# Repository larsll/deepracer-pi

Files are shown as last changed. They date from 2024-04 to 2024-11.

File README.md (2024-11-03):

The effort has moved to [DeepRacer Custom](https://github.com/aws-deepracer-community/deepracer-custom)!

# DeepRacer for Raspberry Pi 4

This repository provides a port of the DeepRacer software stack to the Raspberry Pi 4. It runs
on Ubuntu 22.04 with ROS2 Humble, but with most of original code. To make the image smaller the server image is recommended.

## Features

Main features of the port:

- Previously trained models will work
- Uses Tensorflow Lite or OpenVINO for inference. Supports the Intel Neural Compute Stick 2 (NCS2/MYRIAD)
- Can integrate with DREM
- Single power source¹ - reduces weight and lowers center of gravity
- Over-the-Air Software Updates

## Parts

The following parts are needed:

- Raspberry 4 or compatible board, recommended 4GB or 8GB RAM, but even 1GB will work as memory consumption is about 700MB.
- Optional: [Intel Neural Compute Stick (NCS) 2](https://www.intel.com/content/www/us/en/developer/articles/tool/neural-compute-stick.html)
- [Waveshare Servo Driver Hat](https://www.waveshare.com/product/raspberry-pi/hats/motors-relays/servo-driver-hat.htm) or compatible PCA9865 servo boards.
- USB camera with ~60 deg FOV, e.g. original DeepRacer camera or a Raspberry Pi camera.
- 4 RGB light diodes
- Misc cables

¹ The Waveshare hat comes with a step-down converter from 7.4V to 5V, and will power the Pi via the GPIO header. Other similar cards will require separate power.

**Optional**

- Fan/heat-sink kit for Raspberry PI 4

## Software Install

Installation of software is reasonably straight forward, as pre-built packages are provided:

- Flash an SD card with Ubuntu 22.04 Server for ARM64 using the Raspberry Pi Imager.
- Boot the SD card, and let it upgrade (this takes some time...)
- Run `git clone https://github.com/larsll/deepracer-pi`
- Run `sudo ./install-prerequisites.sh`
- Reboot
- Run `sudo ./install-deepracer.sh`

Once installed you can start the stack with `sudo /opt/aws/deepracer/start_ros.sh`. To ensure a smooth start a camera needs to be plugged in.
The launch log will now display in the console.

To automatically start at boot do `sudo systemctl enable deepracer-core` and to start the service in the background `sudo systemctl start deepracer-core`.

### Changes

Some changes have been made to the code to enable access to GPIO as sysfs layout is different on the Raspberry Pi than on the custom Intel board.

### Improvements

- Stripped down OS
- Runs the custom deepracer stack also seen in [deepracer-scripts](https://github.com/davidfsmith/deepracer-scripts).

### Details

**PWM Outputs**

| Channel | Purpose | Notes |
| --- | --- | --- |
| 0 | Speed controller | <span style="color:red">Remove red cable for stock DeepRacer ESC</span> |
| 1 | Steering servo | |
| 2 | RGB LED | Tail light - Red |
| 3 | RGB LED | Tail light - Green |
| 4 | RGB LED | Tail light - Blue |
| 5 |
| 6 |
| 7 | RGB LED |
| 8 | RGB LED |
| 9 | RGB LED |
| 10 | RGB LED |
| 11 | RGB LED |
| 12 | RGB LED |
| 13 | RGB LED |
| 14 | RGB LED |
| 15 | RGB LED |

<span style="color:red">**NOTE:** Remove the red cable on the stock DeepRacer from the speed controller into PWM channel 0, otherwise you are putting 6V into the servo hat.</span>

LiPo can power both the board and car, 3 pin (balance lead) gets wired to VIN (black and red cables only) to power the board and RPi. The 2 pin power cable goes to the car as normal.

**GPIO layout:**

- `gpio1` - enables PWM (does not do anything, PWM is always on for the Waveshare board)
- `gpio495`-`gpio504` - maps to PWM7 to PWM15 on the Hat, to control three RGB leds (those originally on the side of the board)

**USB host mode:**
To connect the USB-C port on the Raspberry Pi 4 to a USB on your computer, then you need to perform two changes:
* Add `dtoverlay=dwc2,dr_mode=host` to your `/boot/firmware/config.txt`
* Add `modules-load=dwc2,g_ether` to your `/boot/firmware/cmdline.txt`

With this you will see a new network connect appear in Windows (and Mac?). The Raspberry Pi will have IP 10.0.0.1; you can connect to the console via `https://deepracer.aws`. This will require your computer to be disconnected from all other networks (given a DNS priority issue). SSH directly to the IP will work.

## What does not (yet) work

- Battery gauge is not connected - red warning message persists
- Device Info Node is looking in non-existent places - no real impact

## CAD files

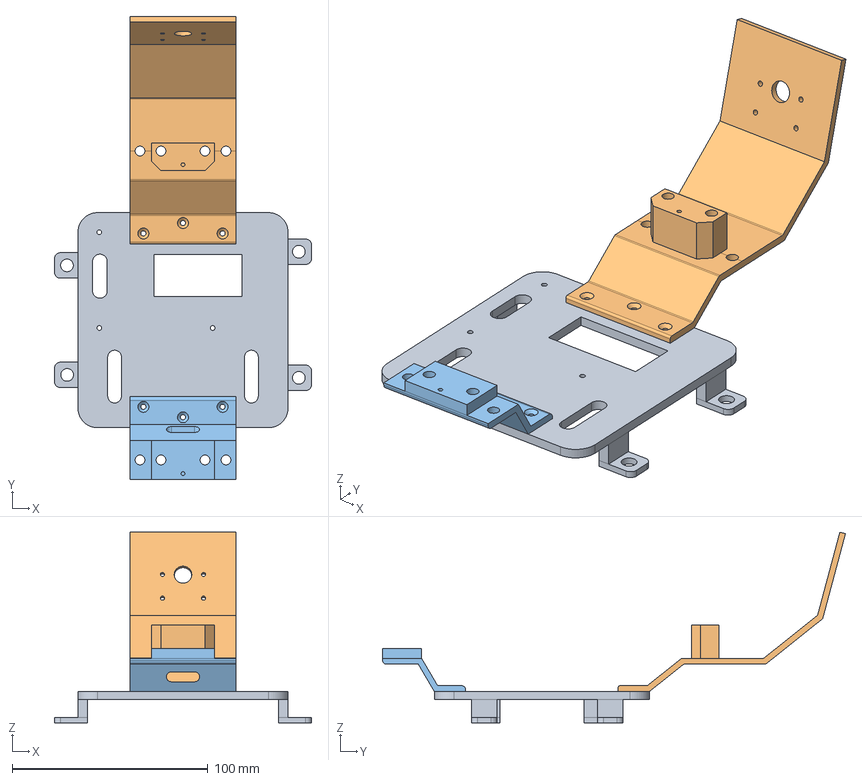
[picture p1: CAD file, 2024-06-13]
drawings/PiMount v1.3.FCStd
131.5 x 236.8 x 97.5 mm
Plate
Front
Back

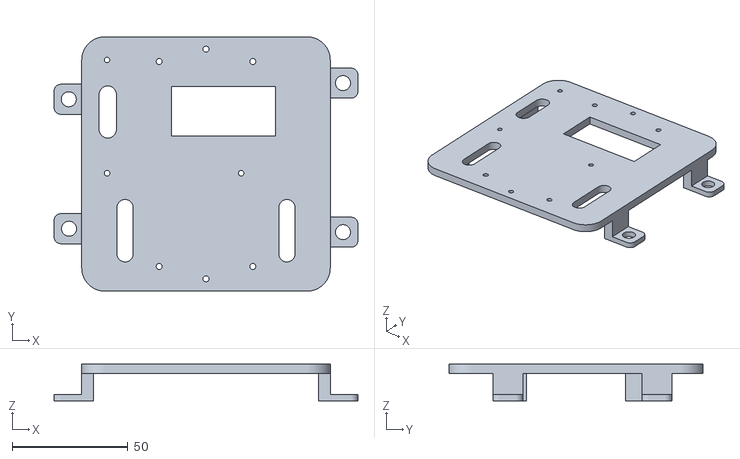
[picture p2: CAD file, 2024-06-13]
drawings/PiMount v1.3-Plate.stl
131.5 x 110.0 x 16.0

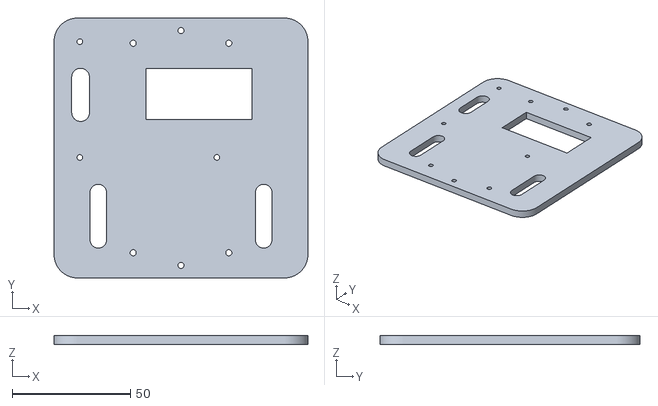
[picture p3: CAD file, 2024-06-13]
drawings/PiMount v1.3-Plate-NoLegs.stl
107.5 x 110.0 x 4.00

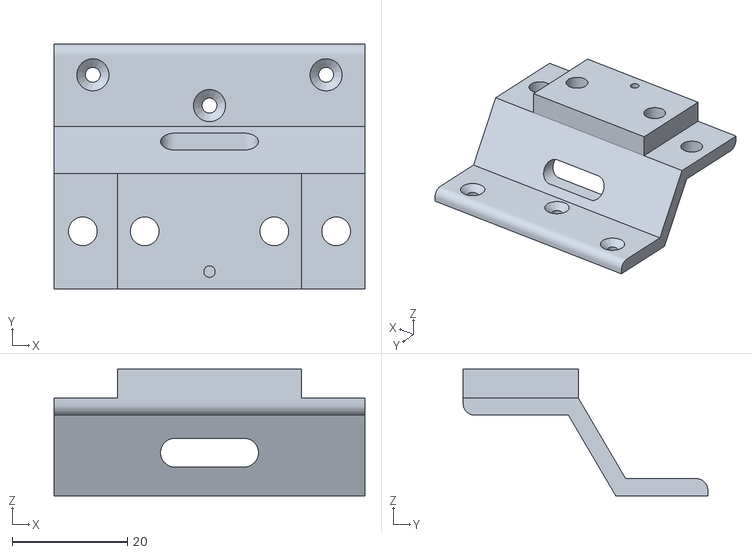
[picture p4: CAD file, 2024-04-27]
drawings/PiMount v1.3-Back.stl
54.0 x 42.5 x 22.0

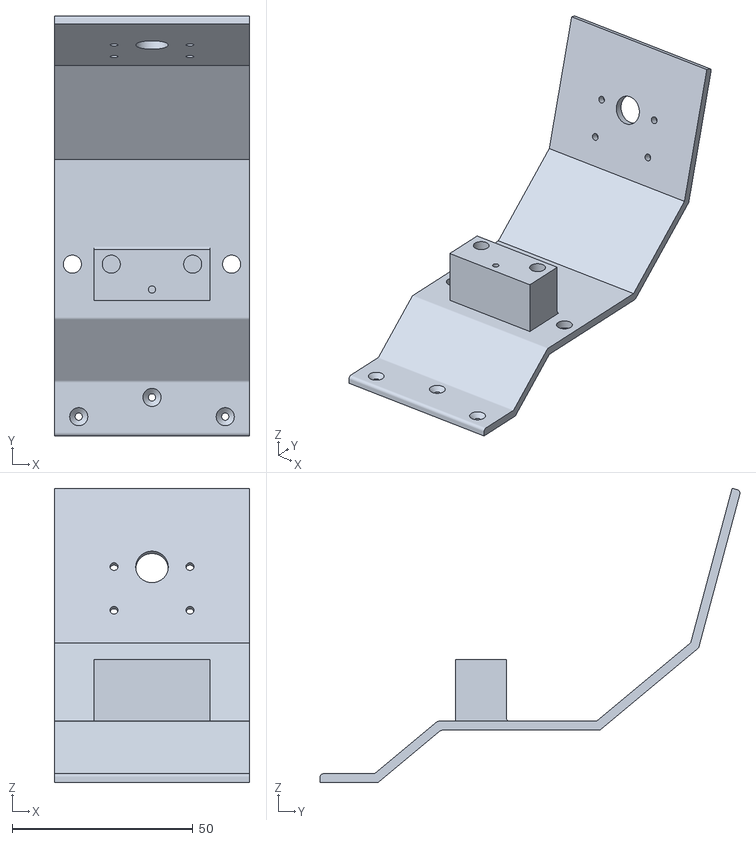
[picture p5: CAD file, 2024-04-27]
drawings/PiMount v1.3-Front.stl
54.0 x 116.1 x 81.4

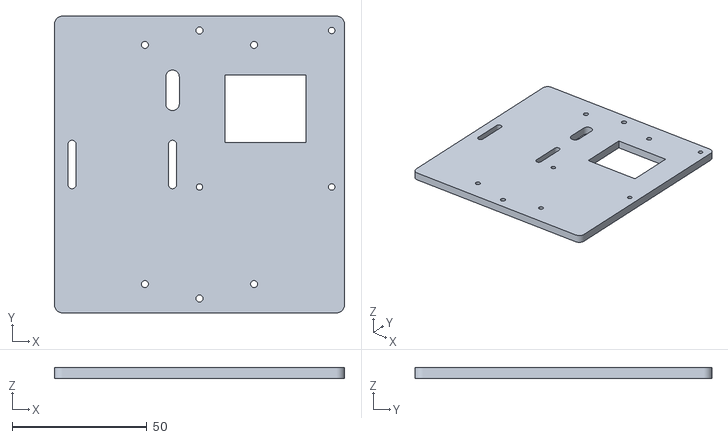
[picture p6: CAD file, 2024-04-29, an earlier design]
drawings/PiMount v1.2-Plate-NoLegs.stl
107.5 x 110.0 x 4.00

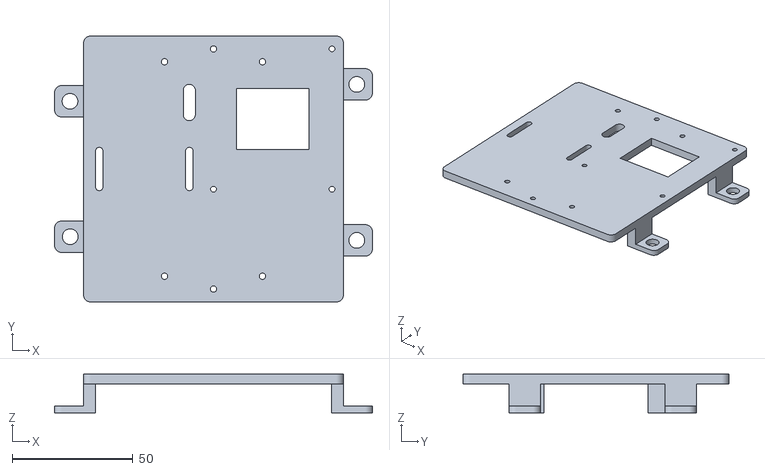
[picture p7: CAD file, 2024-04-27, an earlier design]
drawings/PiMount v1.2-Plate.stl
131.5 x 110.0 x 16.0

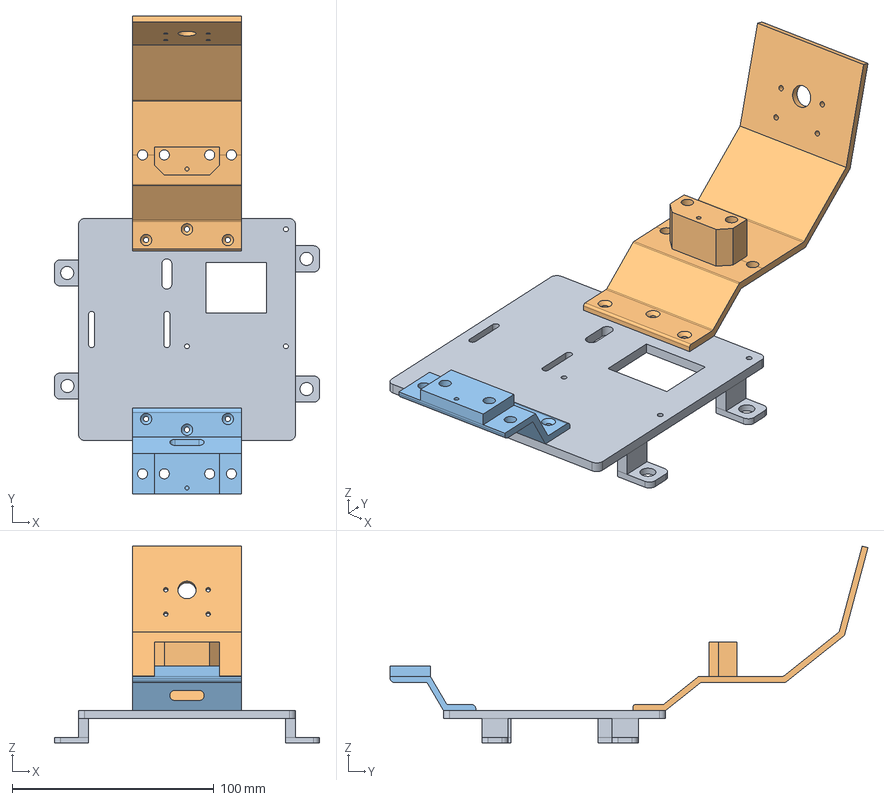
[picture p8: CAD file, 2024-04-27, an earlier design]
drawings/PiMount v1.2.FCStd
131.5 x 236.8 x 97.5 mm
Plate
Front
Back

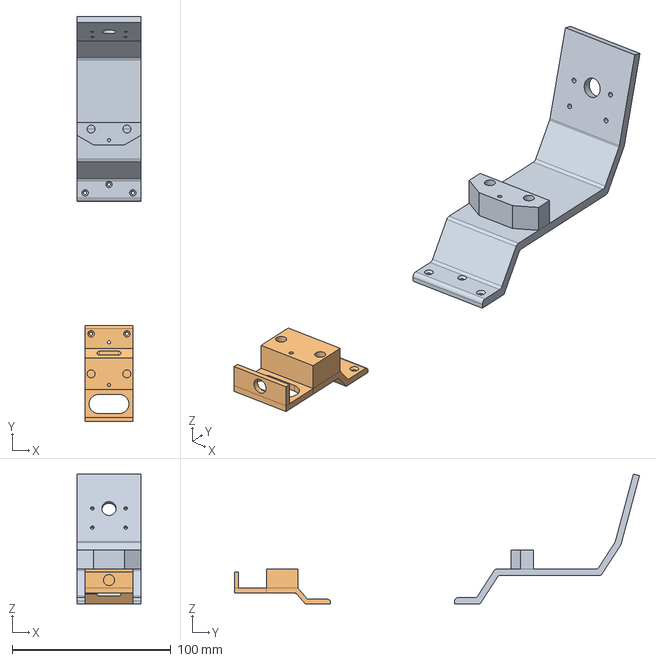
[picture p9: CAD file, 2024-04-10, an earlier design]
drawings/PiMount v1.1.FCStd
40.0 x 254.8 x 81.8 mm
Front
Back

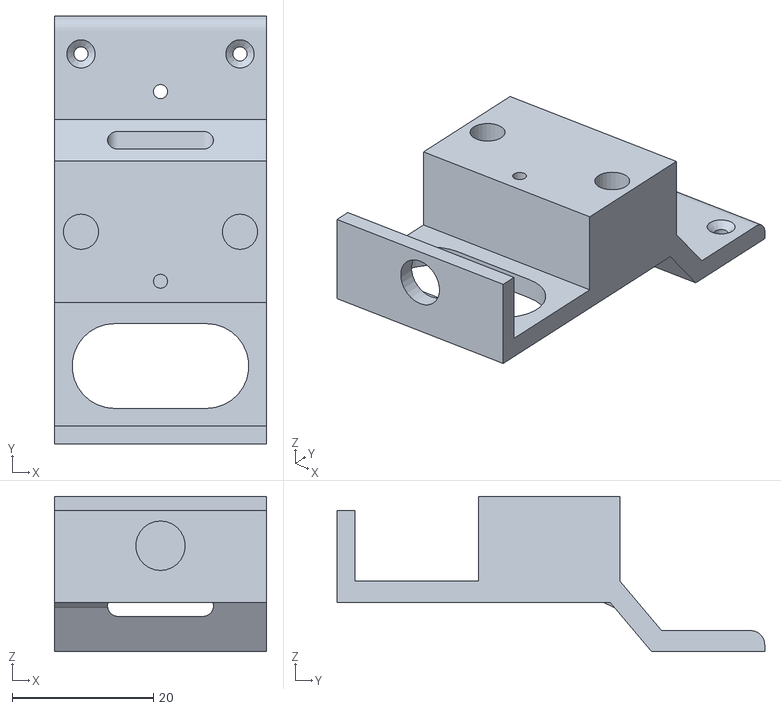
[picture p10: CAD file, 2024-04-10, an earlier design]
drawings/PiMount v1.1-Back.stl
30.0 x 60.5 x 22.0

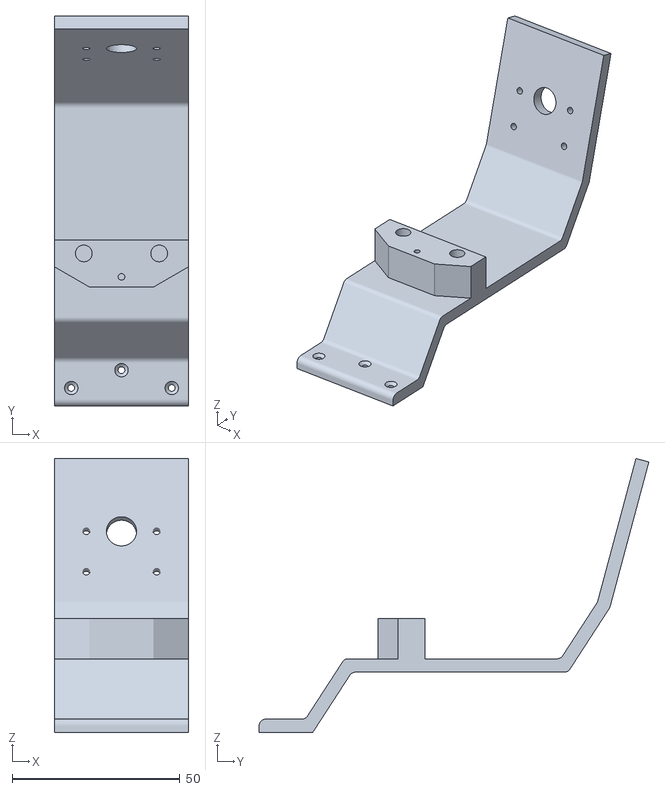
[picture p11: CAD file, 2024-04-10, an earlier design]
drawings/PiMount v1.1-Front.stl
40.0 x 116.3 x 81.8

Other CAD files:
drawings/PiMount v1.1-Plate.stl

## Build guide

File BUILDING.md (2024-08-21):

# Building a Deepracer Pi

* Raspberry Pi 4, recommended 2GB or more of RAM
    * Stand-off set (2.5mm)
* [Waveshare Servo Driver Hat](https://www.waveshare.com/product/raspberry-pi/hats/motors-relays/servo-driver-hat.htm) or compatible PCA9865 servo boards. 
    * Stackable header 40pin (to get higher servo driver hat higher than the fan)
* Raspberry Pi Camera 2
    * Longer cable (20-25cm)
    * Screws M2x15mm + nuts
* Recommended cooling fan: [GeeekPi Raspberry Pi 4 Armor Lite](https://www.amazon.de/gp/product/B091L1XKL6/ref=ppx_yo_dt_b_search_asin_title?ie=UTF8&psc=1)
* RGB Led: 
    * [AZDelivery 5 x KY-016 FZ0455](https://www.amazon.co.uk/AZDelivery-KY-016-3-Colour-Arduino-including/dp/B07V6YSGC9/ref=sr_1_1)
    * 4 female-female jumper cables
    * [Led Holder](https://www.amazon.co.uk/Chanzon-Holder-Headfor-Emitting-Diodes/dp/B083Q9Q1ZR/ref=sr_1_4_sspa)
* Servo extension cable (with red cable cut)
* 3-pin female JST
* 2.5mm plastic screws (preferrably of good quality) to mount back and front; or use M2 screws with nuts

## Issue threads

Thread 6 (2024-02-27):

Abount Hardware,such as camera

Trz-me, 2024-02-27:
Greetings,

Your project has piqued my interest immensely, and I find the prospect of miniaturizing DeepRacer particularly intriguing. Could you please inform me if there are any specific requirements regarding the hardware composition and cable connections for this project?

For instance, is it imperative to use the official DeepLens camera?

The following image depicts a mini DeepRacer model vehicle I previously encountered, which base on  Raspberry Pi.
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

larsll, 2024-02-27:
I have added a Raspberry Pi Camera v2 on mine; it is almost better fitting (more resembling the picture in the simulator) than the one in the original car. The importance is the horizontal field-of-view (60 degrees); and the position (height over track, 15 degrees tilt forward and position ahead of the front tires). You might see some 3d print instructions to fit it onto the WLToys A949, A959, A979 later.

You don't really need any specific cables; but the Servo Hat from Waveshare would be needed. (It is the interface between RPi and the Servo/ESC.)

larsll, 2024-03-12:
Closing as no further discussion.

Closed 2024-03-12.

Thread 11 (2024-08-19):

Compatibility with Raspberry Pi 5?

jeremypedersen, 2024-08-19:
Sorry to contact you via GitHub Issues, but I wasn't able to join the DeepRacer Community Discord (phone verification issue).

Just curious if this code works with the Raspberry Pi 5. I notice the README refers to "Raspberry Pi 4 compatible" boards. Would that include the 5?

larsll, 2024-08-20:
I have not tried. Apparently GPIO works differently on the 5, so I suspect some changes would be needed.

jeremypedersen, 2024-08-21:
Sorry, another quick question. I had a look at the .stl files for the mounting plate and front and back pieces, and it isn't clear which version of the files I should print out for use with the DeepRacer car. After opening them and examining them carefully, I assume I need to print:

PiMount v1.2-Back.stl
PiMount v1.2-Front.stl
PiMount v1.2-Plate.stl

So....all "v1.2". Is that correct?

Also, what mounting hardware did you use to mount the Pi to the plate and to mount the Pi camera? I bought a set of M3/M2.5 bolts, screws, and spacers, not knowing what else to buy.

larsll, 2024-08-21:
You can do either v1.2 or v1.3 plate - the v1.3 plate has the Pi in the front, rotated - v1.2 has it on the right side. Legs if you want to mount on a DeepRacer, no-Legs if you want to mount on stock A947, A959, A979.

Check also - https://github.com/larsll/deepracer-pi/pull/10/files

larsll, 2024-08-21:
> Ok I'll try with the 4 first then (apparently Pi 4 and Pi5 share the same GPIO pinout but use different GPIO hardware supported by different libraries). 👍

The code primarily uses sysfs, so if that works then only the pin numbers need adjusting.

jeremypedersen, 2024-08-21:
Awesome, missed that one.

jeremypedersen, 2024-08-28:
Just a followup: I did test with a Pi 4B and a Waveshare servo driver hat. Worked like a charm. If I get a chance, I will try again later on with a Pi 5.

jeremypedersen, 2024-09-03:
Did some testing on the Raspberry Pi 5 this morning. Turns out Ubuntu Server 22.04 is not supported on the Pi 5 and [there are no plans to back-port it](https://forums.raspberrypi.com/viewtopic.php?t=359566#p2157713).

This means either:

1. Updating the whole ROS 2 stack to work with ROS 2 Jazzy on Ubuntu 24.04
2. Attempting to run ROS 2 Humble on Ubuntu 23, as documented [in this blog post](https://lkseng.github.io/posts/2024/01/07/ros-2-humble-on-raspberrypi-5.html)
3. Attempt to run ROS 2 inside Docker containers running Ubuntu 22

I'll try Option 2 later this week and update here on whether or not it can be made to work. Options 1 and 3 are too much work for me to attempt right now.

As for GPIO incompatibilities, I'm not able to test that yet, but it [does look like sysfs is forwards compatible with the Pi 5](https://forums.raspberrypi.com/viewtopic.php?t=359302), assuming a newer kernel is used.

jeremypedersen, 2024-09-03:
After some additional research it looks like there are enough problems to make Options 2 and 3 unlikely to work.

- Running ROS 2 Humble in Docker on 24.04 can work, but as Docker containers aren't VMs and don't have a normal "boot" process, systemd isn't going to work and NetworkManager probably won't work either.
- Running ROS 2 Humble on Ubuntu 23 *might* work, but Ubuntu 23 uses Python 3.11 not 3.10 and no [deadsnakes](https://github.com/deadsnakes) Python 3.10 is available for Ubuntu 23, meaning it 3.10 would have to be built from source.

So the correct thing to do for the Pi 5 would be to port everything forward to ROS 2 Jazzy on Ubuntu 24.04. Don't have time for that right now but if I find the time I'll definitely give it a try + share my code.

larsll, 2024-09-03:
@jeremypedersen - I think moving to Jazzy is the easiest thing. Foxy to Humble was quite simple; code changes were very limited. The bigger topic was to adapt the DR code to work with the OS (differences between 20.04 and 22.04). For now, as the RPi4 is working this is not really a priority, but still a valid request, so I will keep it open.

larsll, 2024-11-03:
Note; this effort has moved to https://github.com/aws-deepracer-community/deepracer-custom

Closed 2024-11-03.

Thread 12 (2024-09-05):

What does the robot you used look like? Can you help me build mine?

HEITORNERY, 2024-09-05:
I want to build a robot with Raspberry Pi 4 and using ROS 2 Humble, but I didn't find information on your github about the robot you are using. I would like to know if you can help with information about assembling a robot that can use this repository. Images of the robot's circuit, of all the components it needs, of the connections with the robot, that would help a lot.

davidfsmith, 2024-09-05:
Hello - I'm in the process of writing a blog post which details what's needed and how to connect it all up, should be live in the next few days or so - just need to finish it off and retake some photos

HEITORNERY, 2024-09-05:
If possible, I would like the name of this blog and the link to the post. Thank you for your response and I look forward to your post.

davidfsmith, 2024-09-05:
I'll update here once it's published.

larsll, 2024-09-05:
So the parts are partially here:
https://github.com/larsll/deepracer-pi/blob/main/BUILDING.md

It lacks the obvious though; it is a WLToys A979 you build it all on; and you will need a servo. Let's leave this ticket open to update the docs once the blog post is out.

larsll, 2024-11-03:
Note: we have moved to https://github.com/aws-deepracer-community/deepracer-custom

Closed 2024-11-03.

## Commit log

2024-02-11 Note on camera compatibility
2024-02-14 Installer fix and documentation around PWM (#4)
    * Create `dist` directory for packages
    * Adding in notes about PWM and power
    * Added a warning in red about the speed controller
    * Added a warning in red about the speed controller
2024-02-24 Tuning sensor-fusion and install script
2024-04-10 Initial drawings
    [PiMount v1.1-Back.stl, PiMount v1.1-Front.stl, PiMount v1.1-Plate.stl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]
2024-04-14 Dummy Battery Indication
2024-04-16 Renaming to be more logical
    [PiMount v1.1-Front.stl, PiMount v1.1-Plate.stl]
2024-04-27 Version 1.2 of mount.
    [PiMount v1.2-Back.stl, PiMount v1.2-Front.stl, PiMount v1.2-Plate.stl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]
2024-04-29 Plate without legs
    [PiMount v1.2-Plate-NoLegs.stl]
2024-06-13 Rotated layout of the Plate
    [PiMount v1.3-Plate-NoLegs.stl, PiMount v1.3-Plate.stl, PiMount v1.3.FCStd]
2024-10-30 Fix web_video_server reference as ro2 branch is currently broken
2024-10-30 Add the v1.3 front and back for completeness
    [PiMount v1.3-Back.stl, PiMount v1.3-Front.stl]
